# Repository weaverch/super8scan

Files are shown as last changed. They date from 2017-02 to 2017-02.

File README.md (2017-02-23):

------------------
super8scan Project
------------------

Introduction
------------

A hobbyist's (retired accountant) effort to assemble inexpensive processors and camera, assorted small motors, several 3D printed parts and scrap wood into something capable of digitizing a small collection of Super8mm films from the early 70's.  Films have been in a box in the closet unseen for over 35 years, but appear to be in excellent physical condition.

While this is a comparatively low budget effort, sending the reels off to BigBoxStore etc would yield DVDs for substantially less time and $$.  My justification for taking this path is simply to tinker with 3D modelling and printing, lenses & cameras, gears, microcomputers / processors and python.

The result works, but is inefficient and sloppy, containing a number of abandoned paths from past versions.  It is also very "bare bones", with no setup script, no rewind etc.  Not an issue for me given small inventory of film, but definitely an issue for someone needing more throughput.

Mechanically, my choices clearly suffer from Maslow's hammer ("if all you have is a hammer, everything looks like a nail"), except in my case the hammer is a 3d printer.  

I've studied the following similar-ish efforts closely and taken ideas from them all:

- https://github.com/jas8mm/rpitelecine
- https://github.com/jphfilm/rpi-film-capture/wiki
- http://kinograph.cc/
- http://www.sabulo.com/sb/8mm-film/
- https://therobotfish.com/projects/digital-telecine/
- http://www.mets-telecinesystem.co.uk/

Overview
--------

The capture device is freestanding and limited functionally to capturing raw bayer data images of each frame.  Images are saved to the Pi3's microSD system card (128G).  Python code is single threaded at this stage and system runs at a little over 2 seconds / frame.  Film is advanced by a stepper motor's drive wheel with 2mm O-rings set into it and an opposing pinch wheel.  Film tension is maintained by gravity via two arms mounted on potentiometers that ride up/down as film advances. The changing voltage is read by the Arduino to trigger motors connected to the feed and takeup reels.

Stepping to advance film is calculated on the Pi by grabbing the greyscale bayer data image, threshholding (via OpenCV) a small vertical roi where the sprocket hole should in general be found and grabbing the average Y value of the white pixels.  Stepping info sent to Arduino over serial connection to trigger next frame.  This only works on film with black around the sprockets, but that's all I have.  Calculated steps keep each frame's center within 50 pixels or so above /below image center.  

Once capture is complete, microSD card goes via sneakernet to my desktop booted into Arch Linux.  Images copy to desktop's hard drive at approximately 20MBytes / sec which is considerably faster than my wifi network's transfer rate.

Once on the desktop in NTFS partitions, I batch process the raw image sequences into demoisaiced RGB tiff sequences using dcraw.  These images in turn pass through a python script which locates the sprocket hole again and crops relative to the hole's location, saving a 2066x1550 tiff.

I'm currently using DaVinci Resolve (freebie for non-com use version 12.5) in Windows 10 to cut and paste image sequences into video segments and do all color correction, including I hope masking out the purple fringe that's very noticeable against certain backgrounds.  Resolve also has an incredible tracker that makes stabilization dead simple.  From Resolve I output color corrected / stabilized DPX image sequences which are then encoded with ffmpeg.

Gear Used
--------
Freestanding Capture Thing:
- Raspberry Pi 3 with Arducam 5MP OV5647 cam (M12 mount)
- M12 lens; 12mm focal length mounted separately in a threaded tube for magnification and focusing
- Arduino Uno with Adafruit Motor Shield V2 - drives stepper and two DC motors - serial connection / power via Rpi3 USB
- Stepper motor - 12v / 200 steps connected to homemade 16x reduction gear box (awful...buy geared stepper or figure out microstepping on this driver)
- Light source is an 8x2 diy matrix of 5mm clear white leds powered by 4 to 5 volts dc from an adjustable power supply; adjusting voltage allows rough brightness control; diffusion currently from reflected light in something of a leaky integrating sphere

3D Models:
- Freecad; can be a bit fussy.  I'll be using Fusion360 on future projects.
- 3D printing on owned Original Prusa i3 mk2 acquired as kit from Prusa in Prague. 

Results
-------
Image quality varies between dreadful and barely acceptable yet I enjoy seeing the people and places from long ago immensely.  

Samples housed on Youtube:
-------------------------

Scanning underway  https://youtu.be/BP9WV82NFkA

Sample output      https://youtu.be/8DqxQMjq3eE

Acknowledgements
----------------
Thanks to authors of all the projects listed above.  I've tried to acknowledge authors and their copyrights in source files.  If I've missed anything please advise and I will modify immediately.

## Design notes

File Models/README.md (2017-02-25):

Please read the WARNING.txt first !!

Notes re models:
----------------

Software used:

- FreeCAD     http://www.freecadweb.org
- OpenSCAD    http://www.openscad.org

Most models were developed using FreeCAD, an open source 3d CAD parametric modelling program.  I was able to do what I needed with primitives and booleans and a very few sketches.  Threaded pieces in FreeCAD require the Fasteners workbench, which has to be added after installation.  It is great, easy to install, and located at http://theseger.com/projects/2015/06/fasteners-workbench-for-freecad/

Lens extension / focusing tubes use other folks' parametric OpenSCAD scripts.  Install OpenSCAD, open the *.scad files and see the developers' notes.

General Observations:
--------------------
There are vestiges of initial design uncertainty in some models that could be removed now.  For example the camera slider is far longer than necessary due to the fact that earlier camera designs had lenses a few centimeters from the camera sensor.  The elaborate dc motor mounts for the film reels are there because I wasn't certain how I would connect motors to shafts.  Could be simpler.

I've included the gear setup for the stepper.  The gears are there because I needed greater resolution and I was / am too cheap to buy another (geared) stepper.  The gears are awful; I would not take that route from a fresh start.

Model Sets:
-----------

Camera
------
- cameraSledV3.FCStd				                Very tight fit; too long
- camera-m12-slider-mount.FCStd		        Connects cam to sled
- camera-m12.FCStd				                  Arducam 5mp specific

Lenses
------
- FocusFemaleThreadedTube-LongWide.scad
- FocusMaleThreadedTube-LongWide.scad
- m12Internal.FCStd				                Holds lens in MaleTube

Motors Gears Pulleys
--------------------
- dcMount.fcstd					                  Specific to motor used
- dcMotorSlider.FCStd				              Adjust belt tension
- roundbeltpulleyMotor.FCStd			          For 2mm urethane belt
- roundbeltpulleySpool.FCStd			          For 2mm urethane belt

- gear-1.55shaft.FCStd				              Bad idea
- gear-32x8-drive.FCStd				            Bad idea
- gear-8-stepper.FCStd				              For 5mm D shaft
- gearframe.FCStd					                Ignore dummy gears
- gearboxshaft.FCStd
- shaftboardguide.FCStd				            Stabilize driveshaft
- gearedOringRoller.FCStd			            For 2x20mm O rings

- Stepper mount			                      http://www.thingiverse.com/thing:1866886

All Other
---------
- SpoolMount.FCStd				                  Adjust board thickness
- pinchSwingArm.FCStd
- pinchfilmguide.FCStd
- crossbrace.FCStd				                  Brace base & vert panel
- filmsideguide.FCStd				              Threads not used
- filmspoolAdapterSmaller.FCStd		        Holds reels onto shafts
- gate3-top.fcstd					                Mod of RPitelecine
- gate3-bottom.fcstd				                Mod of RPitelecine
- takeupArm.FCStd
- takeupArmBase.FCStd				              Check dimensions of pot
- takeupArmBaseShort.FCStd			            Short version
- potArmspacer.FCStd				                Big 8mm ID washer / guide

- Take-up reel			                        http://www.thingiverse.com/thing:390502

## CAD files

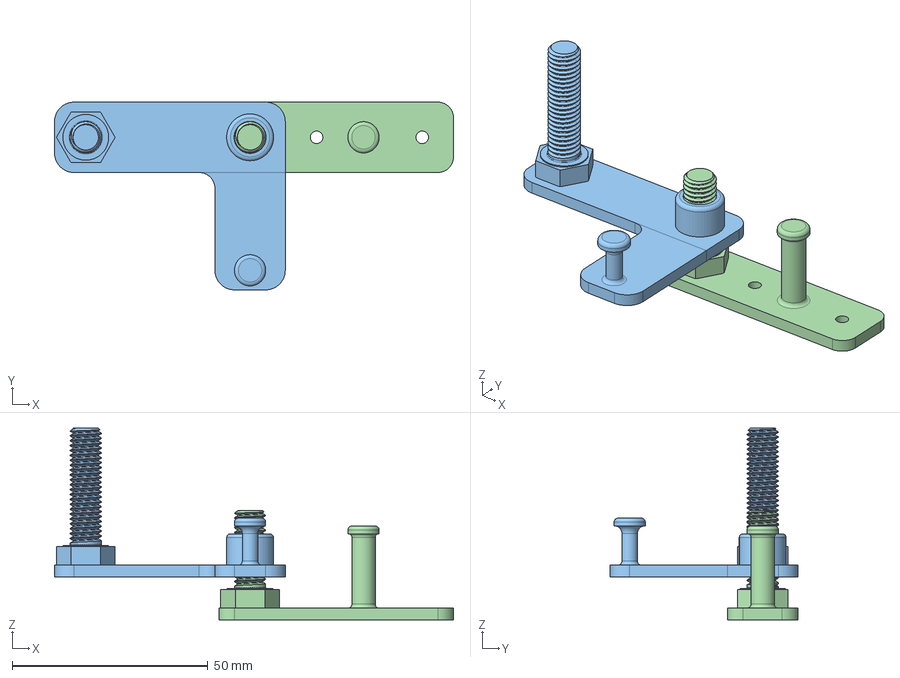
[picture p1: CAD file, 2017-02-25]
Models/AllOther/pinchSwingArm.FCStd
102.0 x 48.0 x 49.0 mm
Arm
Base001
Arm (Solid)
Base001 (Solid)

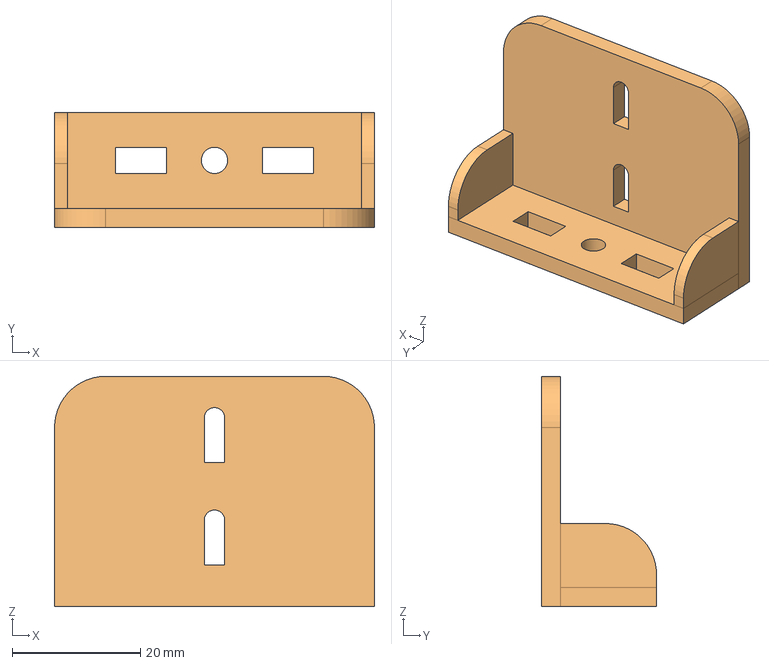
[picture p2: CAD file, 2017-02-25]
Models/Camera/camera-m12-slider-mount.FCStd
50.0 x 18.0 x 36.0 mm
Cut003 (Solid)

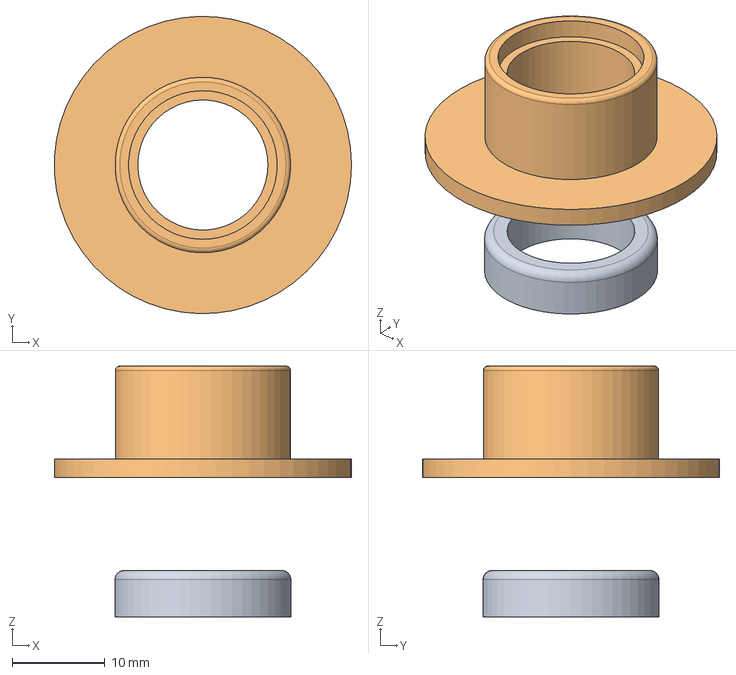
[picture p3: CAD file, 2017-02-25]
Models/Lenses/InternalLensHolder-LongWide.FCStd
32.0 x 32.0 x 27.0 mm
InsideElement
OutsideElement

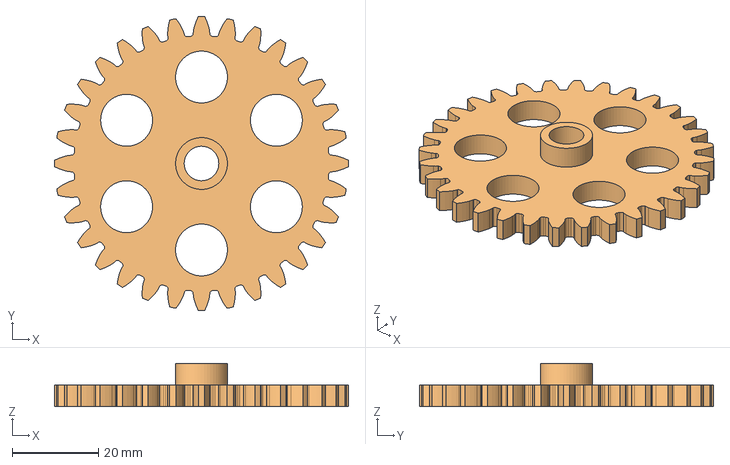
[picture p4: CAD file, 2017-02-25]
Models/MotorsPulleys/gear-32x8-drive.FCStd
68.0 x 68.0 x 10.0 mm
Cut001 (Solid)

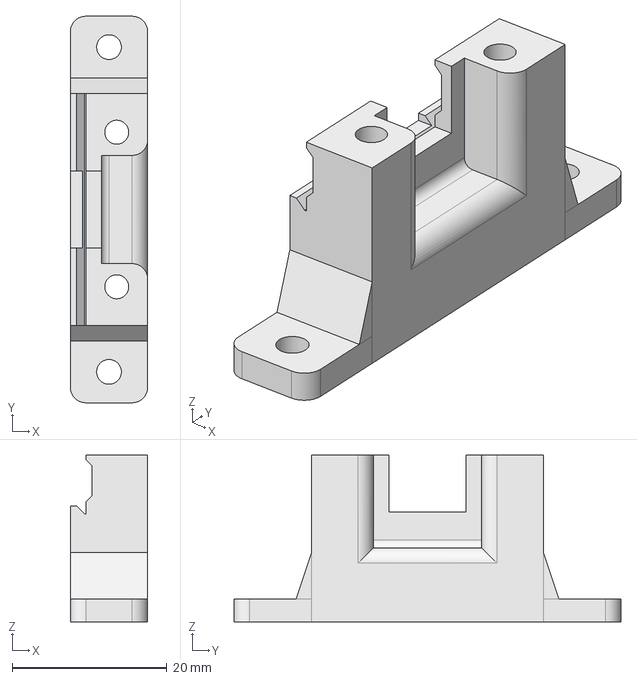
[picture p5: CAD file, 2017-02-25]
Models/AllOther/gate3-bottom.fcstd
10.0 x 50.0 x 21.6 mm

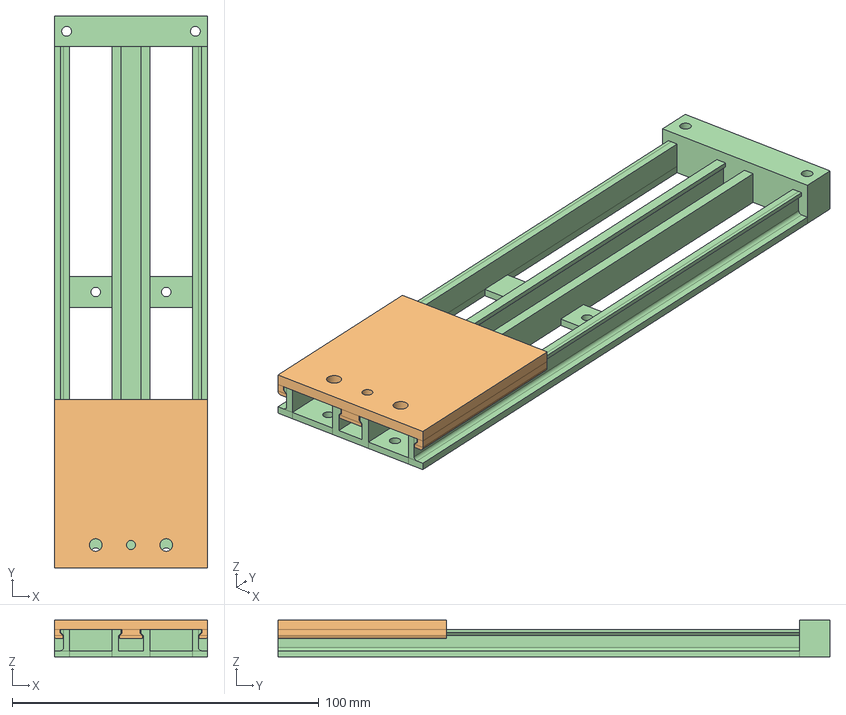
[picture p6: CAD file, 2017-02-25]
Models/Camera/cameraSledV3.FCStd
50.0 x 180.0 x 12.0 mm
SliderAssembly
BedAssembly
BedAssembly (Solid)
SliderAssembly (Solid)

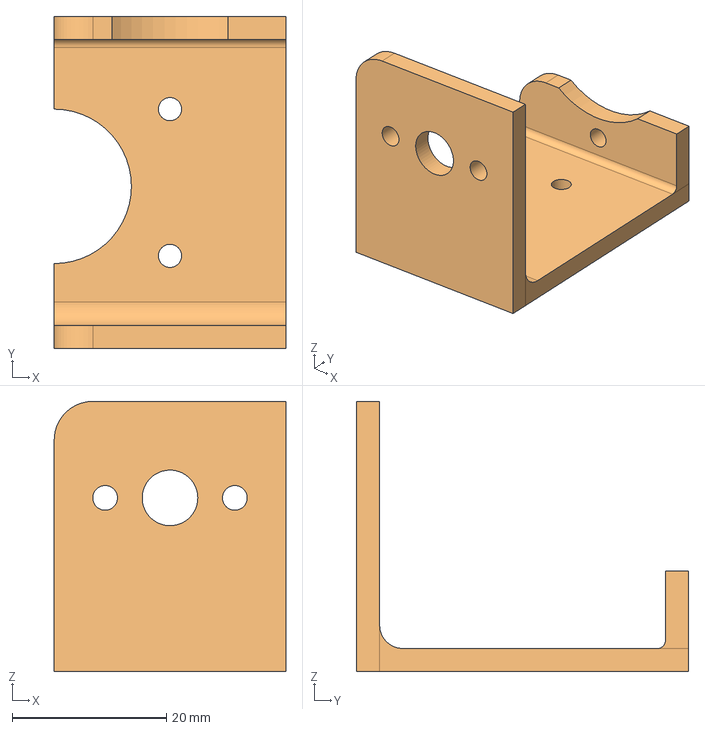
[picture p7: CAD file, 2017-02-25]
Models/MotorsPulleys/dcMount.fcstd
30.0 x 43.0 x 35.0 mm
Fillet003 (Solid)

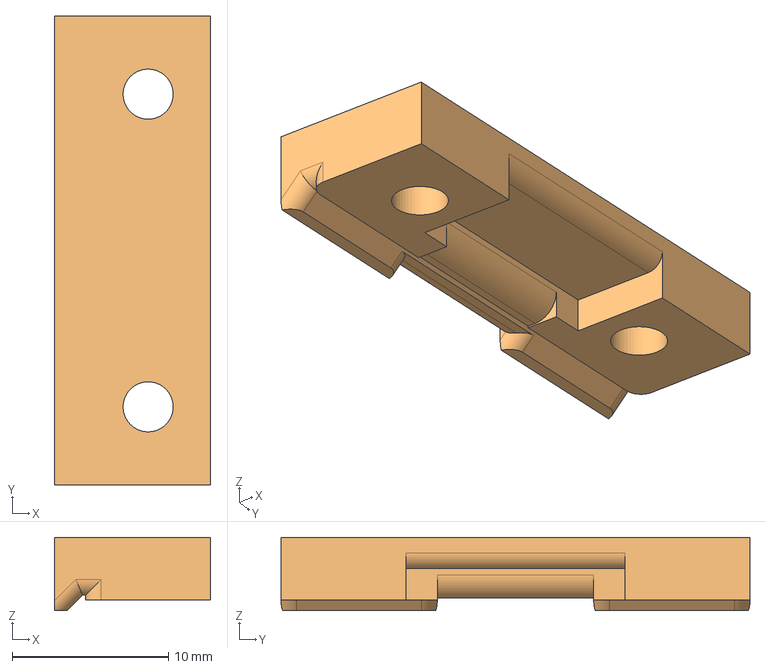
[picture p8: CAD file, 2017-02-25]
Models/AllOther/gate3-top.fcstd
10.0 x 30.0 x 4.70 mm
Top002
Top002 (Solid)

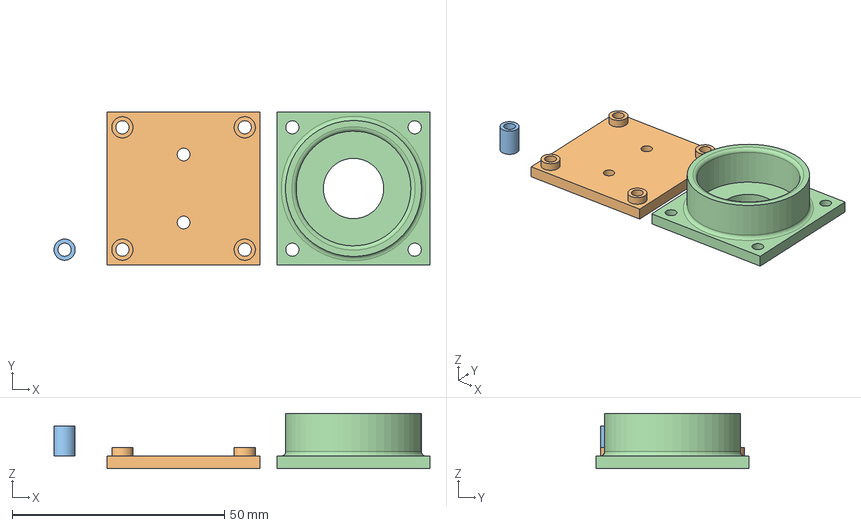
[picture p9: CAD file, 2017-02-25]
Models/Camera/camera-m12.FCStd
88.5 x 36.0 x 13.0 mm
BottomPlate004
TopPlate002
BottomPlateStandoff
BottomPlate004 (Solid)
TopPlate002 (Solid)

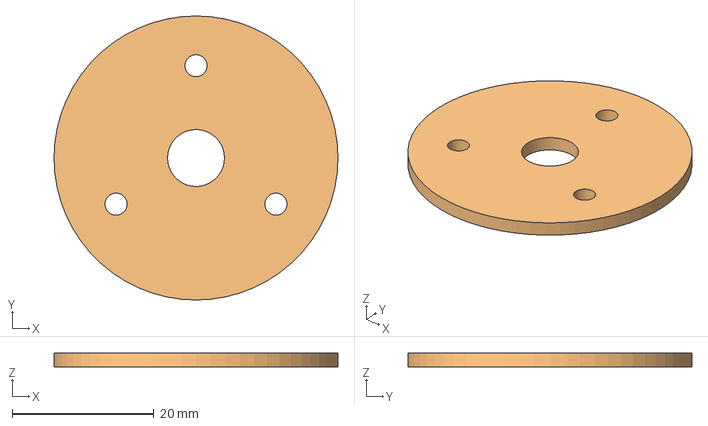
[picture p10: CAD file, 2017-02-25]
Models/MotorsPulleys/shaftboardguide.FCStd
40.0 x 40.0 x 2.00 mm
shaftboardguide
shaftboardguide (Solid)

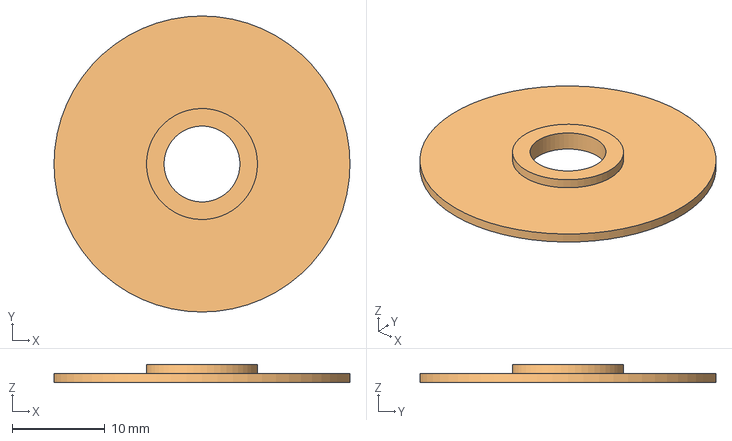
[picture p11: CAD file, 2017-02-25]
Models/AllOther/potArmspacer.FCStd
32.0 x 32.0 x 2.00 mm
PotArmSpacer
PotArmSpacer (Solid)

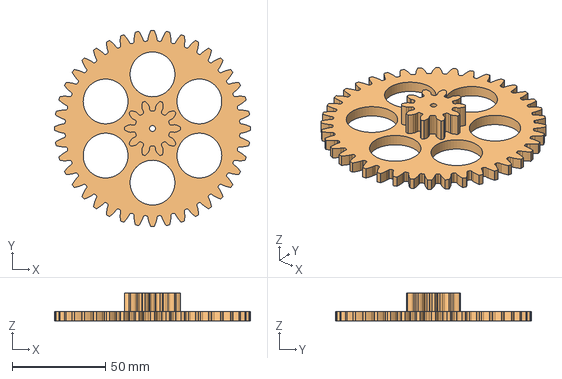
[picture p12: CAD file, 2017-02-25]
Models/MotorsPulleys/gear-1.55shaft.FCStd
105.0 x 105.0 x 15.0 mm
Cut001 (Solid)

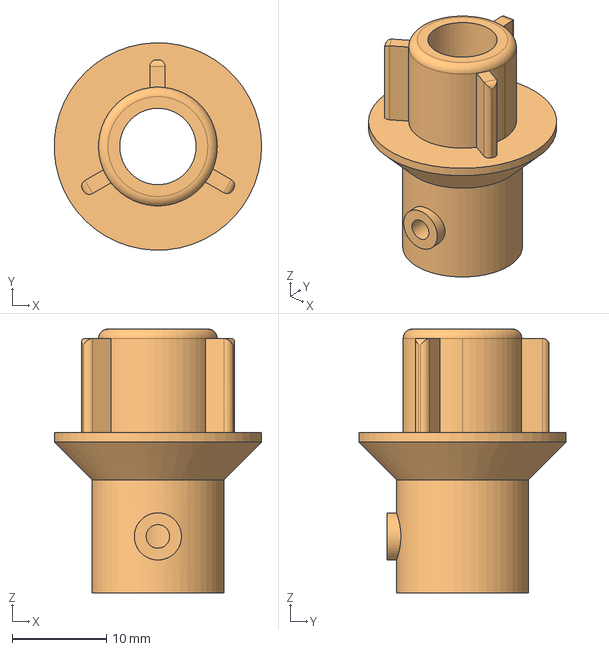
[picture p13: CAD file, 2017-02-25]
Models/AllOther/filmspoolAdapterSmaller.FCStd
22.0 x 22.0 x 28.0 mm
WholeThingy
WholeThingy (Solid)

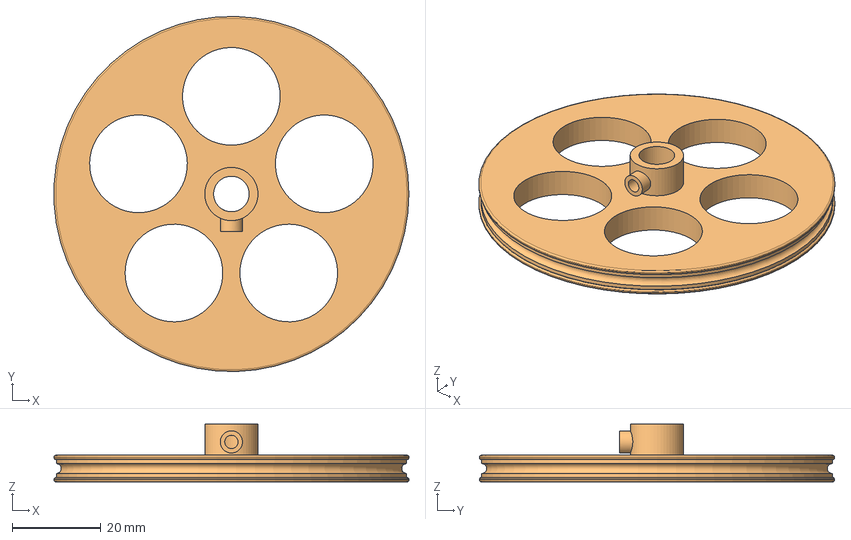
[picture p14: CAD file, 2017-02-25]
Models/MotorsPulleys/roundbeltpulleySpool.FCStd
79.9 x 80.0 x 13.0 mm
Cut003 (Solid)

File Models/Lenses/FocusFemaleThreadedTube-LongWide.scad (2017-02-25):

// ---------------------------------------------------------------
// ThreadedTube.scad
// ---------------------------------------------------------------
//
// Dependencies:
// threads.scad (http://dkprojects.net/openscad-threads/)
//   - metric_thread(diameter, pitch, length);
//
// ---------------------------------------------------------------
// Under the LGPL License
// Author: Hristo Iankov (http://www.thingiverse.com/itzo/about)
// ---------------------------------------------------------------
//
// imported libraries are included directly into the file
// at the bottom of this file.
//include <threads.scad>

/* [Hidden] */
// constants

// end types
END_TYPE_NONE = 0;
END_TYPE_MALE_THREAD = 1;
END_TYPE_FEMALE_THREAD = 2;
THREAD_SHARPENER_HEIGHT = 2;

// resolution
$fn = 50;
//$fa=0.5;
//$fs=0.5;

/* [Main] */
outerDiameter = 27;             // [5:100]
// minimum diameter.  must be less than the outer diameter (overridable by Advanced > middleSectionThickness)
innerDiameter = 20;              // [0:100]
// must be greater than bottom end length + top end length
length = 27;                    // [10:250]
// must be between the inner diameter and the outer diameter
threadDiameter = 23;            // [5:100]
threadPitch = 2;                //
topEndType = 2;                 // [0:no thread,1:male thread,2:female thread]
topEndLength = 26;              // [1:50]
bottomEndType = 0;              // [0:no thread,1:male thread,2:female thread]
bottomEndLength = 1;           // [1:50]

/* [Text] */
messageText = "";   // 
messageFontSize = 6;            // [2:25]
messageStartPosition = 2;       // [0:50]
message = "embossed";           //[embossed,deembossed]
messageIsEmbossed = message == "embossed";  //
messageNumberOfSides = 1;       // [1,2,4]

/* [Advanced] */
// make the female thread diameter this much larger in order to accomodate a good fit
threadTolerance = 1;          //
// this setting overrides innerDiameter for the middle section of the tube (0 - off) This used to prevent material waste.
middleSectionThickness = 0;   // [0:25]

// ----------------
// main/test
// ----------------
threadedTubeWithMessage(outerDiameter, innerDiameter, length,
    threadDiameter, threadPitch, 
    topEndType, topEndLength, bottomEndType, bottomEndLength,
    middleSectionThickness,
    messageText, messageFontSize, messageStartPosition, messageIsEmbossed, 
    messageNumberOfSides);

// ----------------
// modules
// ----------------

// generate a tube with the given parameters
// all measurements are in millimeters.
module tube(outerDiameter, innerDiameter, length) {
    difference() {
        cylinder(h=length, d=outerDiameter);
        translate([0,0,-1]) {
            cylinder(h=length+2, d=innerDiameter);
        }
    }
}

module fullyOuterThreadedTube(threadDiameter, threadPitch, threadLength, 
    innerDiameter) {
    difference() {
        metric_thread(threadDiameter, threadPitch, threadLength);
        translate([0,0,-1]) {
            cylinder(h=threadLength+2, d=innerDiameter);
        }
    }
}

module fullyOuterThreadedTubeWithSharpenedTip(threadDiameter, threadPitch, threadLength,
    innerDiameter) {
    difference() {
        fullyOuterThreadedTube(threadDiameter, threadPitch, threadLength, 
                innerDiameter);
        // make a cutting cone for sharpening the tip of the thread
        translate([0,0,-0.1]) {
            difference() {
                cylinder(h=THREAD_SHARPENER_HEIGHT, 
                    r1 = threadDiameter/2 - threadPitch + 2, 
                    r2 = threadDiameter/2 + threadPitch/2 + 2);
                translate([0,0,-0.1]) {
                    cylinder(h=THREAD_SHARPENER_HEIGHT+0.2, 
                        r1 = threadDiameter/2 - threadPitch, 
                        r2 = threadDiameter/2 + threadPitch/2);
                }
            }
        }
    }
 }
 
 module fullyOuterThreadedTubeWithSharpenedTipAndBase(threadDiameter, threadPitch, threadLength,
    innerDiameter, outerDiameter) {
    baseHeight = 2;
    fullyOuterThreadedTubeWithSharpenedTip(threadDiameter, threadPitch, threadLength,
            innerDiameter);
    // generate the base
    translate([0,0,threadLength]) {
        tube(outerDiameter, innerDiameter, baseHeight);
    }
 }

module fullyInnerThreadedTube(threadDiameter, threadPitch, threadLength, 
    innerDiameter, outerDiameter) {
    difference() {
        cylinder(h=threadLength, d=outerDiameter);
        translate([0,0,-1]) {
            metric_thread(threadDiameter + threadTolerance, threadPitch, threadLength+2);
        }
    }
}

module fullyInnerThreadedTubeWithSharpenedTip(threadDiameter, threadPitch, threadLength, 
    innerDiameter, outerDiameter) {
    difference() {
        fullyInnerThreadedTube(threadDiameter, threadPitch, threadLength, 
                innerDiameter, outerDiameter);
        translate([0,0,-0.1]) {
            cylinder(h=THREAD_SHARPENER_HEIGHT, 
                r1 = threadDiameter/2 + threadPitch/2, 
                r2 = threadDiameter/2 - threadPitch/2);
        }
    }
}

// generate a tube end
module createTubeEnd(endType, length, outerDiameter, innerDiameter, 
    threadDiameter, threadPitch) {
    if(endType == END_TYPE_MALE_THREAD) {
        fullyOuterThreadedTubeWithSharpenedTipAndBase(threadDiameter, 
                threadPitch, length, innerDiameter, outerDiameter);
    } else if(endType == END_TYPE_FEMALE_THREAD) {
        fullyInnerThreadedTubeWithSharpenedTip(threadDiameter, 
                threadPitch, length, innerDiameter, outerDiameter);
    } else {
        // assume END_TYPE_NONE
        tube(outerDiameter, innerDiameter, length);
    }
}

// generate a tube with threaded portions
//
// end types:
// - none (plain tube)
// - male thread
// - female thread
//
// message info:
// - embossed = extruded out
// - debossed = impressed in
//
// restriction:
// - threadDiameter must be between tube inner and outer diameter
// - innerDiameter < threadDiameter - threadPitch
// - outerDiameter > threadDiameter
// - length >= topEndLength + bottomEndLength
//
module threadedTube(outerDiameter, innerDiameter, length,
    threadDiameter, threadPitch, 
    topEndType, topEndLength, bottomEndType, bottomEndLength,
    middleSectionThickness) {
        
    // generate the center of the tube
    // remove the top and bottom peices, added below
    if(length > topEndLength + bottomEndLength) {
        translate([0,0,bottomEndLength]) {
            tube(outerDiameter, 
                    middleSectionThickness > 0 ? outerDiameter - middleSectionThickness*2 : innerDiameter, 
                    length-(topEndLength + bottomEndLength));
        }
    }
        
    // generate the top end of the tube
    if(topEndLength > 0) {
        translate([0,0,length]) {
            rotate([0,180,0]) {
                createTubeEnd(topEndType, topEndLength, outerDiameter, innerDiameter, 
                    threadDiameter, threadPitch);
            }
        }
    }
        
    // generate the bottom end of the tube
    if(bottomEndLength > 0) {
        createTubeEnd(bottomEndType, bottomEndLength, outerDiameter, innerDiameter, 
                threadDiameter, threadPitch);
    }
}
 
module generateTubeMessage(messageText, messageFontSize, messageStartPosition,
    outerDiameter, bottomEndLength) {
    rotate([0,0,-90]) { // bring th etext to the front face
        translate([outerDiameter/2-1.5,messageFontSize/2,bottomEndLength + messageStartPosition]) {
            rotate([180,-90,0]) {
                linear_extrude(2) {
                    text(text=messageText, size=messageFontSize);
                }
            }
        }
    }
}

module generateTubeMessageMultipleSides(messageText, messageFontSize, messageStartPosition,
    outerDiameter, bottomEndLength, numberSides) {
    angleIterator = 
        (numberSides == 4) ? [0:90:360] :
        (numberSides == 2) ? [0:180:180] :
        [0:90:80];
        
    for(angle = angleIterator) {
        rotate([0,0,angle]) {
            generateTubeMessage(messageText, messageFontSize, messageStartPosition,
                    outerDiameter, bottomEndLength);
        }
    }
}
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

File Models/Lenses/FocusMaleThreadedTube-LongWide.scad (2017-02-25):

// ---------------------------------------------------------------
// ThreadedTube.scad
// ---------------------------------------------------------------
//
// Dependencies:
// threads.scad (http://dkprojects.net/openscad-threads/)
//   - metric_thread(diameter, pitch, length);
//
// ---------------------------------------------------------------
// Under the LGPL License
// Author: Hristo Iankov (http://www.thingiverse.com/itzo/about)
// ---------------------------------------------------------------
//
// imported libraries are included directly into the file
// at the bottom of this file.
//include <threads.scad>

/* [Hidden] */
// constants

// end types
END_TYPE_NONE = 0;
END_TYPE_MALE_THREAD = 1;
END_TYPE_FEMALE_THREAD = 2;
THREAD_SHARPENER_HEIGHT = 2;

// resolution
$fn = 50;
//$fa=0.5;
//$fs=0.5;

/* [Main] */
outerDiameter = 32;             // [5:100]
// minimum diameter.  must be less than the outer diameter (overridable by Advanced > middleSectionThickness)
innerDiameter = 19;              // [0:100]
// must be greater than bottom end length + top end length
length = 27;                    // [10:250]
// must be between the inner diameter and the outer diameter
threadDiameter = 23.6;            // [5:100]
threadPitch = 2;                //
topEndType = 0;                 // [0:no thread,1:male thread,2:female thread]
topEndLength = 1;              // [1:50]
bottomEndType = 1;              // [0:no thread,1:male thread,2:female thread]
bottomEndLength = 26;           // [1:50]

/* [Text] */
messageText = "";   // 
messageFontSize = 6;            // [2:25]
messageStartPosition = 2;       // [0:50]
message = "embossed";           //[embossed,deembossed]
messageIsEmbossed = message == "embossed";  //
messageNumberOfSides = 1;       // [1,2,4]

/* [Advanced] */
// make the female thread diameter this much larger in order to accomodate a good fit
threadTolerance = 1;          //
// this setting overrides innerDiameter for the middle section of the tube (0 - off) This used to prevent material waste.
middleSectionThickness = 0;   // [0:25]

// ----------------
// main/test
// ----------------
threadedTubeWithMessage(outerDiameter, innerDiameter, length,
    threadDiameter, threadPitch, 
    topEndType, topEndLength, bottomEndType, bottomEndLength,
    middleSectionThickness,
    messageText, messageFontSize, messageStartPosition, messageIsEmbossed, 
    messageNumberOfSides);

// ----------------
// modules
// ----------------

// generate a tube with the given parameters
// all measurements are in millimeters.
module tube(outerDiameter, innerDiameter, length) {
    difference() {
        cylinder(h=length, d=outerDiameter);
        translate([0,0,-1]) {
            cylinder(h=length+2, d=innerDiameter);
        }
    }
}

module fullyOuterThreadedTube(threadDiameter, threadPitch, threadLength, 
    innerDiameter) {
    difference() {
        metric_thread(threadDiameter, threadPitch, threadLength);
        translate([0,0,-1]) {
            cylinder(h=threadLength+2, d=innerDiameter);
        }
    }
}

module fullyOuterThreadedTubeWithSharpenedTip(threadDiameter, threadPitch, threadLength,
    innerDiameter) {
    difference() {
        fullyOuterThreadedTube(threadDiameter, threadPitch, threadLength, 
                innerDiameter);
        // make a cutting cone for sharpening the tip of the thread
        translate([0,0,-0.1]) {
            difference() {
                cylinder(h=THREAD_SHARPENER_HEIGHT, 
                    r1 = threadDiameter/2 - threadPitch + 2, 
                    r2 = threadDiameter/2 + threadPitch/2 + 2);
                translate([0,0,-0.1]) {
                    cylinder(h=THREAD_SHARPENER_HEIGHT+0.2, 
                        r1 = threadDiameter/2 - threadPitch, 
                        r2 = threadDiameter/2 + threadPitch/2);
                }
            }
        }
    }
 }
 
 module fullyOuterThreadedTubeWithSharpenedTipAndBase(threadDiameter, threadPitch, threadLength,
    innerDiameter, outerDiameter) {
    baseHeight = 2;
    fullyOuterThreadedTubeWithSharpenedTip(threadDiameter, threadPitch, threadLength,
            innerDiameter);
    // generate the base
    translate([0,0,threadLength]) {
        tube(outerDiameter, innerDiameter, baseHeight);
    }
 }

module fullyInnerThreadedTube(threadDiameter, threadPitch, threadLength, 
    innerDiameter, outerDiameter) {
    difference() {
        cylinder(h=threadLength, d=outerDiameter);
        translate([0,0,-1]) {
            metric_thread(threadDiameter + threadTolerance, threadPitch, threadLength+2);
        }
    }
}

module fullyInnerThreadedTubeWithSharpenedTip(threadDiameter, threadPitch, threadLength, 
    innerDiameter, outerDiameter) {
    difference() {
        fullyInnerThreadedTube(threadDiameter, threadPitch, threadLength, 
                innerDiameter, outerDiameter);
        translate([0,0,-0.1]) {
            cylinder(h=THREAD_SHARPENER_HEIGHT, 
                r1 = threadDiameter/2 + threadPitch/2, 
                r2 = threadDiameter/2 - threadPitch/2);
        }
    }
}

// generate a tube end
module createTubeEnd(endType, length, outerDiameter, innerDiameter, 
    threadDiameter, threadPitch) {
    if(endType == END_TYPE_MALE_THREAD) {
        fullyOuterThreadedTubeWithSharpenedTipAndBase(threadDiameter, 
                threadPitch, length, innerDiameter, outerDiameter);
    } else if(endType == END_TYPE_FEMALE_THREAD) {
        fullyInnerThreadedTubeWithSharpenedTip(threadDiameter, 
                threadPitch, length, innerDiameter, outerDiameter);
    } else {
        // assume END_TYPE_NONE
        tube(outerDiameter, innerDiameter, length);
    }
}

// generate a tube with threaded portions
//
// end types:
// - none (plain tube)
// - male thread
// - female thread
//
// message info:
// - embossed = extruded out
// - debossed = impressed in
//
// restriction:
// - threadDiameter must be between tube inner and outer diameter
// - innerDiameter < threadDiameter - threadPitch
// - outerDiameter > threadDiameter
// - length >= topEndLength + bottomEndLength
//
module threadedTube(outerDiameter, innerDiameter, length,
    threadDiameter, threadPitch, 
    topEndType, topEndLength, bottomEndType, bottomEndLength,
    middleSectionThickness) {
        
    // generate the center of the tube
    // remove the top and bottom peices, added below
    if(length > topEndLength + bottomEndLength) {
        translate([0,0,bottomEndLength]) {
            tube(outerDiameter, 
                    middleSectionThickness > 0 ? outerDiameter - middleSectionThickness*2 : innerDiameter, 
                    length-(topEndLength + bottomEndLength));
        }
    }
        
    // generate the top end of the tube
    if(topEndLength > 0) {
        translate([0,0,length]) {
            rotate([0,180,0]) {
                createTubeEnd(topEndType, topEndLength, outerDiameter, innerDiameter, 
                    threadDiameter, threadPitch);
            }
        }
    }
        
    // generate the bottom end of the tube
    if(bottomEndLength > 0) {
        createTubeEnd(bottomEndType, bottomEndLength, outerDiameter, innerDiameter, 
                threadDiameter, threadPitch);
    }
}
 
module generateTubeMessage(messageText, messageFontSize, messageStartPosition,
    outerDiameter, bottomEndLength) {
    rotate([0,0,-90]) { // bring th etext to the front face
        translate([outerDiameter/2-1.5,messageFontSize/2,bottomEndLength + messageStartPosition]) {
            rotate([180,-90,0]) {
                linear_extrude(2) {
                    text(text=messageText, size=messageFontSize);
                }
            }
        }
    }
}

module generateTubeMessageMultipleSides(messageText, messageFontSize, messageStartPosition,
    outerDiameter, bottomEndLength, numberSides) {
    angleIterator = 
        (numberSides == 4) ? [0:90:360] :
        (numberSides == 2) ? [0:180:180] :
        [0:90:80];
        
    for(angle = angleIterator) {
        rotate([0,0,angle]) {
            generateTubeMessage(messageText, messageFontSize, messageStartPosition,
                    outerDiameter, bottomEndLength);
        }
    }
}
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

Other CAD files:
Models/AllOther/crossbrace.FCStd
Models/MotorsPulleys/gearedOringRoller.FCStd
Models/AllOther/takeupArm.FCStd
Models/MotorsPulleys/gear-8-stepper.FCStd
Models/AllOther/SpoolMount.FCStd
Models/AllOther/filmsideguide.FCStd
Models/AllOther/pinchfilmguide.FCStd
Models/AllOther/takeupArmBase.FCStd
Models/AllOther/takeupArmBaseShort.FCStd
Models/MotorsPulleys/dcMotorSlider.FCStd
Models/MotorsPulleys/gearboxshaft.FCStd
Models/MotorsPulleys/gearframe.FCStd
Models/MotorsPulleys/roundbeltpulleyMotor.FCStd
Models/MotorsPulleys/stepperOringRoller.FCStd

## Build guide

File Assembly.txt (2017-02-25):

Assembly Notes:
---------------

Useful words and images go here....

Parts & Sources:

- BoltDepot.com
- McMaster
- surplusshed.com
- M12lenses.com
- Amazon

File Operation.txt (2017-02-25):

Operation Notes:
----------------

To come...

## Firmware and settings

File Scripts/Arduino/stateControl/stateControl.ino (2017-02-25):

#include <Adafruit_NeoPixel.h>
#include <Wire.h>
#include <Adafruit_MotorShield.h>
#include "utility/Adafruit_MS_PWMServoDriver.h"


#define PIN 6
#define NUM_LEDS 7
uint8_t BRIGHTNESS = 50;
int gamma[] = {
  0,  0,  0,  0,  0,  0,  0,  0,  0,  0,  0,  0,  0,  0,  0,  0,
  0,  0,  0,  0,  0,  0,  0,  0,  0,  0,  0,  0,  1,  1,  1,  1,
  1,  1,  1,  1,  1,  1,  1,  1,  1,  2,  2,  2,  2,  2,  2,  2,
  2,  3,  3,  3,  3,  3,  3,  3,  4,  4,  4,  4,  4,  5,  5,  5,
  5,  6,  6,  6,  6,  7,  7,  7,  7,  8,  8,  8,  9,  9,  9, 10,
  10, 10, 11, 11, 11, 12, 12, 13, 13, 13, 14, 14, 15, 15, 16, 16,
  17, 17, 18, 18, 19, 19, 20, 20, 21, 21, 22, 22, 23, 24, 24, 25,
  25, 26, 27, 27, 28, 29, 29, 30, 31, 32, 32, 33, 34, 35, 35, 36,
  37, 38, 39, 39, 40, 41, 42, 43, 44, 45, 46, 47, 48, 49, 50, 50,
  51, 52, 54, 55, 56, 57, 58, 59, 60, 61, 62, 63, 64, 66, 67, 68,
  69, 70, 72, 73, 74, 75, 77, 78, 79, 81, 82, 83, 85, 86, 87, 89,
  90, 92, 93, 95, 96, 98, 99, 101, 102, 104, 105, 107, 109, 110, 112, 114,
  115, 117, 119, 120, 122, 124, 126, 127, 129, 131, 133, 135, 137, 138, 140, 142,
  144, 146, 148, 150, 152, 154, 156, 158, 160, 162, 164, 167, 169, 171, 173, 175,
  177, 180, 182, 184, 186, 189, 191, 193, 196, 198, 200, 203, 205, 208, 210, 213,
  215, 218, 220, 223, 225, 228, 231, 233, 236, 239, 241, 244, 247, 249, 252, 255
};

int takeupPotTrigger = 900;
int takeupPotKiller = 950;
int feedPotTrigger = 755;
int feedPotKiller = 675;
bool takeupDCMotorRunning = false;
bool feedDCMotorRunning = false;

// the possible states of the state-machine
typedef enum {  NONE, GOT_L, GOT_S, GOT_X } states;

// current state-machine state
states state = NONE;
// current partial number
unsigned int currentValue;

Adafruit_MotorShield AFMS = Adafruit_MotorShield();
Adafruit_StepperMotor *myStepper = AFMS.getStepper(200, 1);
Adafruit_DCMotor *takeupDCMotor = AFMS.getMotor(4);
Adafruit_DCMotor *feedDCMotor = AFMS.getMotor(3);
Adafruit_NeoPixel strip = Adafruit_NeoPixel(NUM_LEDS, PIN, NEO_GRBW + NEO_KHZ800);

void handlePreviousState ()
{
  switch (state)
  {
    case GOT_L:
//      processLED (currentValue);
      break;
    case GOT_S:
      processStepper (currentValue);
      break;
    case GOT_X:
      processStopAll (currentValue);
      break;
  }  // end of switch

  currentValue = 0;
}  // end of handlePreviousState

void processIncomingByte (const byte c)
{
  if (isdigit (c))
  {
    currentValue *= 10;
    currentValue += c - '0';
  }  // end of digit
  else
  {

    // The end of the number signals a state change
    handlePreviousState ();

    // set the new state, if we recognize it
    switch (c)
    {
      case 'L':
        state = GOT_L;
        break;
      case 'S':
        state = GOT_S;
        break;
      case 'X':
        state = GOT_X;
        break;
      default:
        state = NONE;
        break;
    }  // end of switch on incoming byte
  } // end of not digit

} // end of processIncomingByte

//void processLED (const unsigned int value)
//{
//  if (value == 1) {
//    for (uint16_t i = 0; i < strip.numPixels(); i++) {
//      strip.setPixelColor(i, strip.Color(0, 0, 0, 255));
//    }
//    strip.show();
//  }
//  else if (value == 0) {
//    for (uint16_t i = 0; i < strip.numPixels(); i++) {
//      strip.setPixelColor(i, strip.Color(0, 0, 0, 0));
//    }
//    strip.show();
//  }
//} // end of processLED

void processStepper (const unsigned int value)
{
  myStepper->step(value, BACKWARD, DOUBLE);
  Serial.println("M");
} // end of processStepper

void processStopAll (const unsigned int value)
{
  takeupDCMotor->run(RELEASE);
  feedDCMotor->run(RELEASE);
  myStepper->release();
} // end of processStartStop


void setup() {
  Serial.begin(115200);

  state = NONE;

  AFMS.begin();  // create with the default frequency 1.6KHz
  myStepper->setSpeed(100);  // 10 rpm
  takeupDCMotor->setSpeed(25);
  takeupDCMotor->run(RELEASE);
  feedDCMotor->setSpeed(25);
  feedDCMotor->run(RELEASE);
  strip.setBrightness(BRIGHTNESS);
  strip.begin();
//  processLED(0);
}

void loop() {

  int potValuetakeup = analogRead(A1);

  if (potValuetakeup < takeupPotTrigger)
  {
    if (!takeupDCMotorRunning) {
//      Serial.println("Motor Run");
      takeupDCMotor->run(FORWARD);
      takeupDCMotorRunning = true;
    }
  }

  if (potValuetakeup > takeupPotKiller) {
    if (takeupDCMotorRunning) {
//      Serial.println("Motor Stop");
      takeupDCMotor->run(RELEASE);
      takeupDCMotorRunning = false;
    }
  }


  int potValuefeed = analogRead(A2);

  if (potValuefeed > feedPotTrigger)
  {
    if (!feedDCMotorRunning) {
//      Serial.println("Motor Run");
      feedDCMotor->run(FORWARD);
      feedDCMotorRunning = true;
    }
  }

  if (potValuefeed < feedPotKiller) {
    if (feedDCMotorRunning) {
//      Serial.println("Motor Stop");
      feedDCMotor->run(RELEASE);
      feedDCMotorRunning = false;
    }
  }

  while (Serial.available ())
    processIncomingByte (Serial.read ());

}

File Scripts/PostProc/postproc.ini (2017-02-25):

[Camera]
###########################
# Attributes not at default
###########################
shutter_speed = 32000
resolution_w = 640
resolution_h = 480
iso = 100
awb_modes = off
awb_red_gain = 1.54
awb_blue_gain = 1.04
sharpness = 0
brightness = 50
exposure_modes = off
exposure_compensation = 0
drc_strength = off
raw_formats = bgr
image_denoise = False
########################
# Attributes at defaults
########################
contrast = 0
saturation = 0
color_effects = none
rotation = 0
hflip = False
vflip = False
zoom = 0.0,0.0,1.0,1.0
stereo_modes = none
clock_modes = reset
image_effects = none
meter_modes = average
video_stabilization = False
flash_modes = off

[PerfCrop]
westXROI = 200
incrXROI = 5
northYROI = 500
incrYROI = 1000
pixelsPerStep    = 9
minWhitePixels   = 1800
maxWhitePixels   = 2500
sprocketCntrDist = 160
cropXOrigin = 380
cropXWidth = 2066
cropYBand = 775
